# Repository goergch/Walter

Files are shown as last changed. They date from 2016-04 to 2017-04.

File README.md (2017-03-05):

# Walter
Walter is a self-made, dangerous, industrial robot with 6 DOF. Right in the middle of development. Check the [Documentation](http://walter.readthedocs.io). Contact me via the [hackaday page](https://hackaday.io/post/53678).

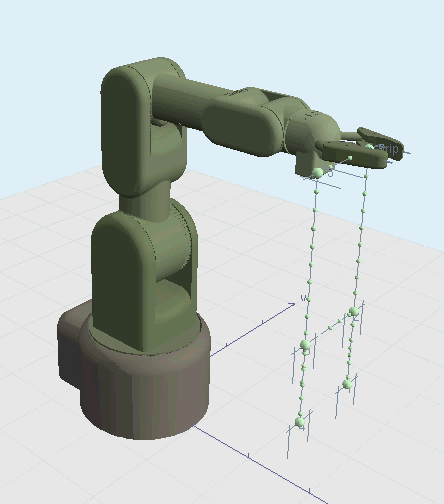
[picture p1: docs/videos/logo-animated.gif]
work in progress


### Contents
    /cad 	    CAD designs (TurboCAD)
    /theory     mainly kinematics
    /code       code of Cortex, Trajectory Planner, and Webserver  
    /schematics schematics of Cortex and its power board
    /docs		source of Walter's [Documentation](https://http://walter.readthedocs.io)
    /datasheets datasheets of components Walter is made of

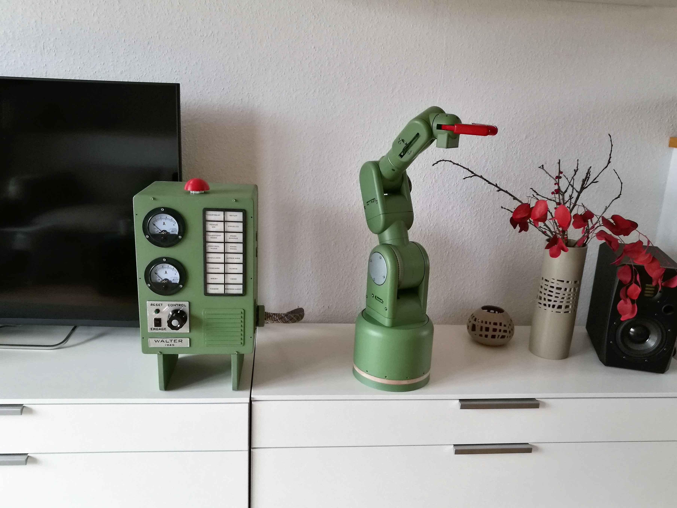
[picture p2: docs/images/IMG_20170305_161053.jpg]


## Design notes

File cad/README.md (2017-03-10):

All CAD  files made with TurboCAD. Due to a performance issue with TurboCAD, the working sources with geometric parts are stored in [intermediate](https://github.com/jochenalt/Walter/blob/master/cad/intermediate). The final objects (ACIS objects only) are stored here. In [simplified](https://github.com/jochenalt/Walter/blob/master/cad/simplified) the objects used within Walters UI (displayed in OpenGL) are located. They omit many details in order to speed up the UI. [Wiki](https://github.com/jochenalt/Walter/blob/master/cad/wiki) contains the CAD explosion drawings used in the documentation.

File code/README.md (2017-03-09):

C++ source code of Walter

* [Cortex](https://github.com/jochenalt/Walter/blob/master/code/BotCortex) 
contains the C++ Teensy code interpolating a given trajectory and running the closed loop for all actuators
* [GLUI](https://github.com/jochenalt/Walter/blob/master/code/GLUI) 
old GLUI framework to enhance openGL by buttons, labels etc.  Used by WalterPlanner.
* [freeglut](https://github.com/jochenalt/Walter/blob/master/code/freeglut) 
old library used by GLUI
* [Common](https://github.com/jochenalt/Walter/blob/master/code/WalterCommon) 
Common parts used by Cortex and Webserver, especially containing the communication protocol in between
* [Kinematics](https://github.com/jochenalt/Walter/blob/master/code/WalterKinematics) 
Library used by Webserver and Planning UI computing kinematics and trajectories
* [WalterPlanner](https://github.com/jochenalt/Walter/blob/master/code/WalterPlanner) 
OpenGL UI for planning trajectories and sending the Webserver
* [WalterServer](https://github.com/jochenalt/Walter/blob/master/code/WalterServer) 
Webserver receiving running on Odroid XU4 receiving commands from WalterPlanner
* [ServerOdroid](https://github.com/jochenalt/Walter/blob/master/code/ServerODroid) 
To be deleted, used before WalterServer was  portable for Windows and Linux

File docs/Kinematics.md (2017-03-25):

Kinematics is about computation of the tool-centre-point (*TCP*) out of joint angles and vice versa. First is simple, latter is more tricky, but lets see later on.
But before starting any kinematics, it is necessary to define all coordinate systems.

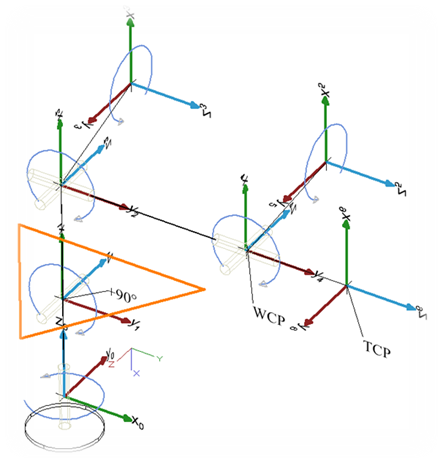
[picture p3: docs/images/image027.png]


The most important design decision is to let the three upper axis’ intersect in one point, the so-call wrist-center-point (*WCP*). This decision makes the computation of the inverse kinematic solvable without numeric approaches.

The picture shows the used coordinate systems in the default position of the bot, having all angles at 0°, starting from the base (angle<sub>0</sub>) and ending with the coordinate system of the hand (angle<sub>6</sub>). For convenience the forearm (angle<sub>1</sub>) adds +90° to the real angle in order to have the base position at 0° of the bot, although the illustrated actually is -90°. The coordinate systems have been are arranged according to the Denavit Hardenberg convention, which is:

The transformation from angle<sub>i</sub> to angle<sub>i+1</sub> is given via 

1. rotation around the x-axis by α

2. translation along the x-axis by α

3. translation along the z-axis by *d*, and

4. rotation around the z-axis by θ

So, the Denavit Hardenberg parameters are:

| Joint | a[°]  | a[mm] | d[mm] |
|---  | ---| --- | --- |
| Hip | *-90°*| *0* | *d<sub>0</sub>* |
| Upper arm  | *0* | *a<sub>1</sub>*  | *0* |
| Forearm | *-90°*| *0* | *0* |
| Elbow | *90°* | *0* | *d<sub>3</sub>* |
| Wrist | *-90°*| *0* | *0* |
| Hand | *0* | *0* | *d<sub>5</sub>* |

The general definition of a Denavit Hardenberg (DH) transformation is

&nbsp;&nbsp;&nbsp;&nbsp;

which is a homogeneous matrix with two rotations *(x,z)* and two translations *(x,z)*.

Combined with the DH parameters, the following DH matrixes define the transformation from one joint to its successor:













## Forward Kinematics

With the DH transformation matrixes at hand, computation of the bot’s pose (i.e the position and orientation of the gripper) out of the joint angles is straight forward. The matrix representing the gripper’s pose  is 

&nbsp;&nbsp;&nbsp;&nbsp; 

By multiplying the transformation matrix with the origin (as homogeneous vector), we get the absolute coordinates of the tool centre point in world coordinate system (i.e. relative to the bot’s base).

&nbsp;&nbsp;&nbsp;&nbsp;

The orientation in terms of roll/nick/yaw of the tool centre point can be derived out of by taking the part representing the rotation matrix (). ([Wikipedia Roll/Nick/Yaw](https://de.wikipedia.org/wiki/Roll-Nick-Gier-Winkel#Berechnung_aus_Rotationsmatrix) )

&nbsp;&nbsp;&nbsp;&nbsp;

&nbsp;&nbsp;&nbsp;&nbsp;  
&nbsp;&nbsp;&nbsp;&nbsp;  
&nbsp;&nbsp;&nbsp;&nbsp;  

For  we have a singularity (*atan2* never becomes this), but wikipedia has a solution for that as well
	
&nbsp;&nbsp;&nbsp;&nbsp;
&nbsp;&nbsp;&nbsp;&nbsp;

if  we get

&nbsp;&nbsp;&nbsp;&nbsp;
&nbsp;&nbsp;&nbsp;&nbsp;

Note: Unfortunately, the gripper’s coordinate system is not appropriate for human interaction, since the default position as illustrated in the [Coordinate Systems](images/image027.png) is not nick/roll/yaw=(0,0,0). So, in the Trajectory Visualizer it is handy to rotate the gripper matrix such that the default position becomes (0,0,0). The according rotation matrix represents a rotation of -90° along *x*,*y*, and *z*, done by the rotation matrix

&nbsp;&nbsp;&nbsp;&nbsp;

In the following equations, this is not considered, since it is for convenience in the UI only, so you will find that additional rotation in the source code only. 

## Inverse Kinematics 
Inverse kinematics denotes the computation of all joint angles out of the tool-centre-point’s position and orientation. In general this is hard, and giving a non iterative solution for a 6DOF robot is only feasable, when computation of the grippers position and the grippers orientation can be considered separately, i.e. the angles of the lower three actuators is not depending on the orientation of the gripper. Still, I do not like numerical solutions, even though with todays processors (or FPGAs) this is no more a question of computational power. I just think that a numerical solution is not a real solution but a surrender to complexity. That's why I let the upper three joint angles intersect in the WCP, which is a basic assumption of the following. 

Input of inverse kinematics is the TCP’s position and orientation in terms of roll, nick, yaw, abbreviated by *γ*, *β*,and *α*.





First, we need to compute the wrist-centre-point out the tool-centre-point. This is possible by taking the TCP and moving it back along the TCP’s orientation by the hand length. For doing so, we need the transformation matrix from the base to the last joint  
which we can derive out of the TCP’s position and orientation.

To build the transformation matrix  we need the rotation matrix defining the orientation of the TCP. This is given by multiplying the rotation matrixes for all axis (*γ*, *β*, *α*) which gives  (see also *[computation of rotation matrix out of Euler Angles](http://kos.informatik.uni-osnabrueck.de/download/diplom/node26.html)*).

&nbsp;&nbsp;&nbsp;&nbsp;

Now we can denote the transformation matrix of the TCP by building a homogenous matrix out of *TCP<sub>orientation</sub>* and *TCP<sub>position</sub>*:

&nbsp;&nbsp;&nbsp;&nbsp;

From the TCP’s perspective, WCP is just translated by *d<sub>5</sub>*:

&nbsp;&nbsp;&nbsp;&nbsp;

Furthermore, , so we get the WCP by

&nbsp;&nbsp;&nbsp;&nbsp;

in world coordinates.

Having a top view on the robot shows how to compute the first angle *θ<sub>0</sub>*:

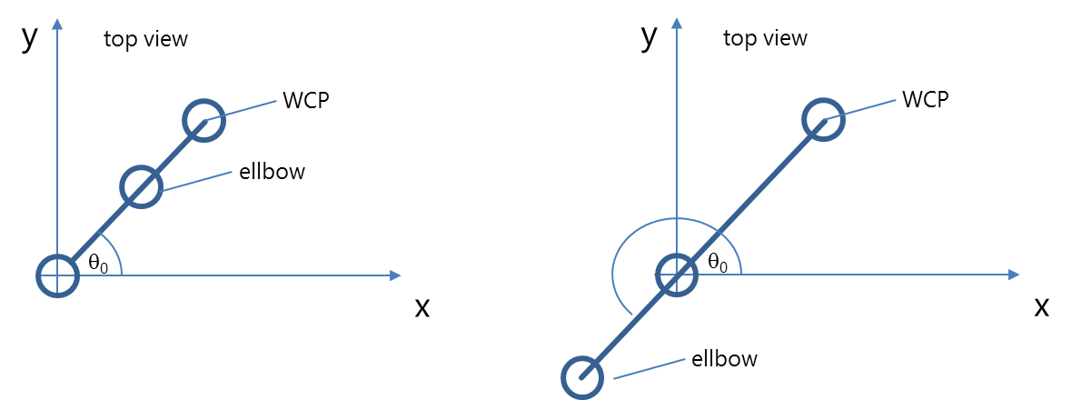
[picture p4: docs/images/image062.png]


&nbsp;&nbsp;&nbsp;&nbsp;

Actually, this angle exists in two variants: if the bot looks backwards, we get the formula above. But another valid solution is looking backward when we get 

&nbsp;&nbsp;&nbsp;&nbsp;

Thanks to the design having a wrist-centre-point where the axes of the three upper actuators intersect, the next two angles can be computed by the triangle denoted in orange:



Again, there are two solutions (aka configurations), one configuration corresponds with a natural pose of the elbow, solution II is a rather unhealthy position:

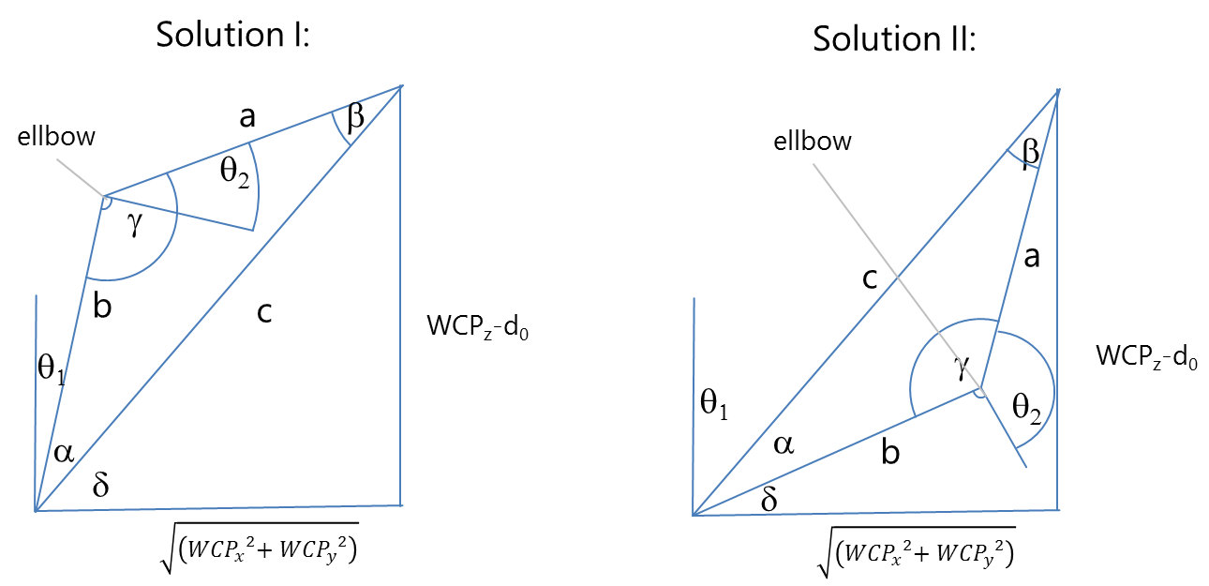
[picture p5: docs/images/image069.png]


*a* and *b* is given by the length of the actuators *a<sub>1</sub>* und *d<sub>3</sub>*. So, with cosine law we get the angles *α* and *γ*.

&nbsp;&nbsp;&nbsp;&nbsp;

&nbsp;&nbsp;&nbsp;&nbsp;
	
Finally, we get


	

and the second solution 

&nbsp;&nbsp;&nbsp;&nbsp;
&nbsp;&nbsp;&nbsp;&nbsp;	

The upper angles *θ<sub>4</sub>*, *θ<sub>5</sub>*, *θ<sub>5</sub>* can be obtained by considering the chain of transformation matrixes. With

&nbsp;&nbsp;&nbsp;&nbsp;	

we get

&nbsp;&nbsp;&nbsp;&nbsp;	

To ease the annoying multiplication  we only need to consider the rotation part of the homogenous matrixes, translation is no more relevant, since the orientation alone defines the three upper angles. 

&nbsp;&nbsp;&nbsp;&nbsp;	

 - and therefore the rotation part  - is already known resp. can be obtained out of the given angles *θ<sub>0</sub>*, *θ<sub>1</sub>*, *θ<sub>2</sub>* by
	
&nbsp;&nbsp;&nbsp;&nbsp;	

By equalizing the previous two equations we get a bunch of equations defining the upper angles, still these equations are hard to solve, due to the complex combination of trignometric functions. But, there are some equations which are simpler and can be solved for an angle. First angle that seems to be easily computable is *θ<sub>4</sub>*:

&nbsp;&nbsp;&nbsp;&nbsp;	

gives two solutions

&nbsp;&nbsp;&nbsp;&nbsp;	

For *θ<sub>3</sub>* there is no easy matrix element, but we can combine

&nbsp;&nbsp;&nbsp;&nbsp;	
&nbsp;&nbsp;&nbsp;&nbsp;		

to

&nbsp;&nbsp;&nbsp;&nbsp;		

which ends up in

&nbsp;&nbsp;&nbsp;&nbsp;		

again having two solutions depending on *θ<sub>4</sub>*. Same is done on *θ<sub>5</sub>*:

&nbsp;&nbsp;&nbsp;&nbsp;		

If *θ<sub>4</sub>=0*, we have an infinite number of solutions *θ<sub>3</sub>* and *θ<sub>5</sub>* (gimbal lock). In that case, we consider   :		

&nbsp;&nbsp;&nbsp;&nbsp;.		

Since we know the trigonometric addition theorem from school

&nbsp;&nbsp;&nbsp;&nbsp;		

we get

&nbsp;&nbsp;&nbsp;&nbsp;		

We are free to choose *θ<sub>3</sub>* and arbitrarily select the bot’s current angle *θ<sub>3</sub>*, such that this one will not move in that specific case.

&nbsp;&nbsp;&nbsp;&nbsp;		
 
In the end, we get eight solutions by combining the possible pose configurations of  *θ<sub>0</sub>*(forward/backward), *θ<sub>1</sub>* and *θ<sub>2</sub>*(triangle flip), and *θ<sub>4</sub>*(hand orientation turn).

The correct solution is chosen by taking the one that differs the least from the current bot’s joint angles. 
What is with all the other equations from ? We could use them to invalidate some of the four solutions, but still there will remain a list of solutions we need to choose from. So, it does not really make sense to take this route.

The selection algorithm is quite simple:

1. consider only mechanically valid solutions, i.e. omit those that violate mechanical boundaries.

2. Compute an angle-wise "*distance*" to the current position and take the solution with the least distance, i.e. take the solution with the least movement.

The latter has the consequence that the pose will try to remain in a configuration and no sudden movements like a turn of 180° happens.

All this is implemented in [Kinematics.cpp](https://github.com/jochenalt/Walter/blob/master/code/WalterKinematics/src/Kinematics.cpp). But - as usual - trying out before implementing this is a good idea, so I did that in this [spreadsheet](https://github.com/jochenalt/Walter/blob/master/theory/Kinematik.xlsx).

Speaking of configurations: if you want to change the configuration of the bot, e.g. from elbow down to elbow up which includes turning the base by 180° the approach of having a linear movement from one pose to the other and interplating in between does not work anymore, since the start and end poses are identical, but with a different configuration.

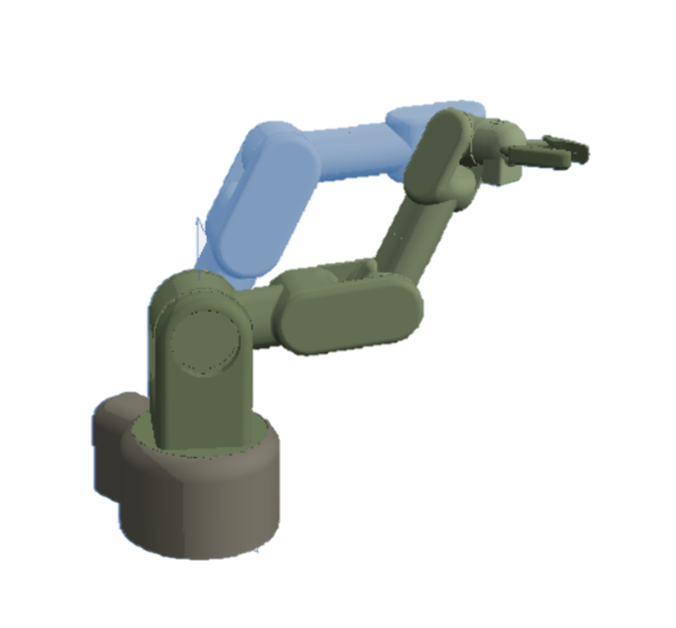
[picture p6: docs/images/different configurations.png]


First possibility to change configuration is to have a non-linear movement that interpolates angle-wise resulting in a weired movement that would be really dangerous in a real world:

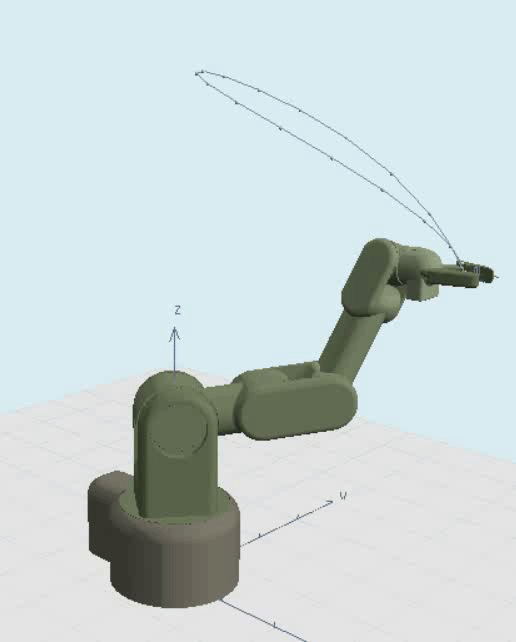
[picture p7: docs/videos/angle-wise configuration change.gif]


So, you rather introduce an intermediate pose where you can safely turn the critical actuator (mostly the shoulder). This is not less expansing, but a more controlled way:

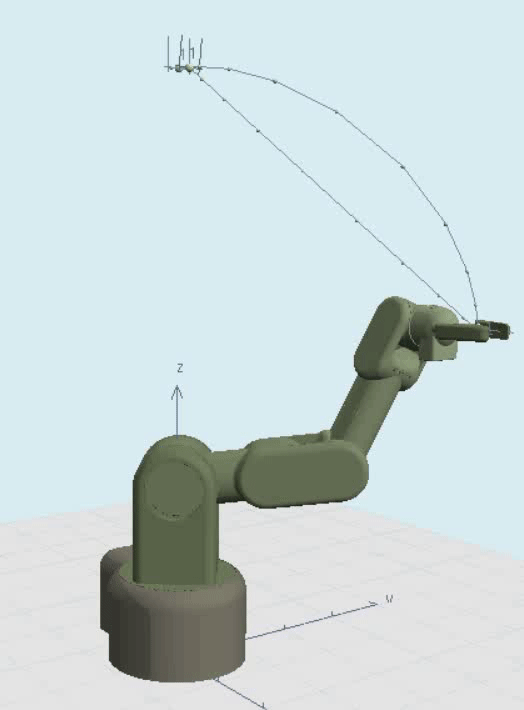
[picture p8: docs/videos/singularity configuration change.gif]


Thing is, that one has to go via a singularity (the upright position) which is normally avoided like hell. One reason is the way how we compute *θ<sub>4</sub>=0*, and a numerical reason that singularities are kind of a black hole, the closer you get, the more you are sucked into imprecisions of floating numbers since you approach poles of the underlying functions. So it is defininitely best to simply avoid changing configurations or getting too close to singularities.

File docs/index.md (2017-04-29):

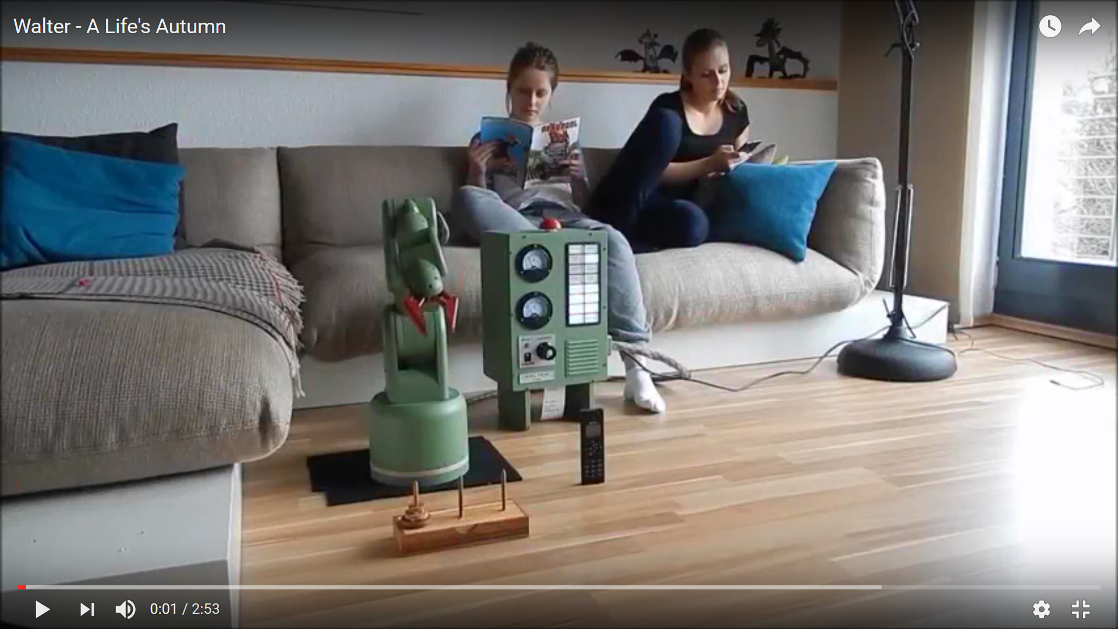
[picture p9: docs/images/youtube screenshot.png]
(http://www.youtube.com/watch?v=XK3WcrrcC8U)


Since man built the first robot, he wanted it to look like himself. I want to make Walter look vintage, and as little DIY as possible, so no visible humps or bulges with motors or gearboxes, nor horrible cables hanging everywhere. Reminds me too much of my dentist. 

Most of the DIY robots are using servos, mostly for convenience, since the encoder is built-in already and they are easy to control. Thing is, when it comes to higher torque, the connection of the servo with the actuator becomes difficult, and hard to make of 3D printed material. If the servo or the flange moves just a little bit within the housing, the according play will magnify to a significant amount at the end of the actuator. An The required precision to avoid this is way above hobby grade components. 


And servos are boringly easy to use. No fun in construction. A motor with a belt drive and a separate angle sensor solves this, it provides low backlash and allows the electronics to compensate imprecise parts with the sensor placed separately from the motor. Additionally, the motor of an actuator can be placed in the previous joint, lowering the centre of gravity of each actuator.

When a belt drive is set, choice comes naturally to stepper motors, since an additional gearbox is not necessary anymore, torque is high and the belts should compensate the vibrations coming from the stepping nature of these motors.

I started with an openGL application simulating the construction.

Now, Walter looks like this, in a beautiful arrangement with selected flowers:


Software part is not easy and especially time-consumung. Most robot makers stop as soon as the limps are moving, which always looks unfinished. But, making the full stack including trajectory planning means four months of work when you have weekends only, of which some parts are really difficult (inverse kinematics). The data flow of the full stack looks like this:

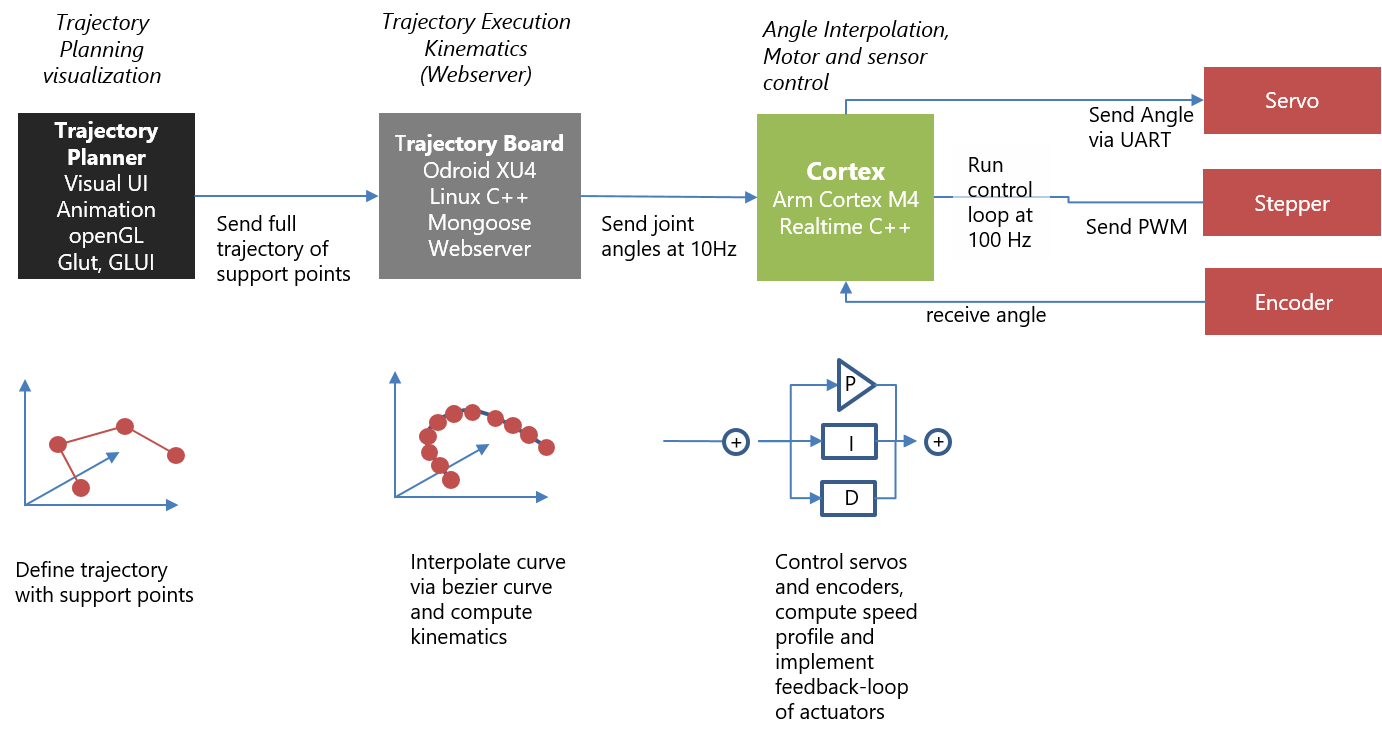
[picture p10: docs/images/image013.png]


We have:

* [Trajectory Planner](./Trajectory) ([source code](https://github.com/jochenalt/Walter/tree/master/code/WalterPlanner))
This is a UI for planning trajectories. All animated gifs in this wiki are made with it. Trajectories are planned by defining single support points. After planning is done, the trajectory is transfered to the

* [Trajectory Execution](./Webserver) ([source code](https://github.com/jochenalt/Walter/tree/master/code/WalterServer)). This component consists of a webserver that runs trajectories by interpolating Bézier curves betweeen support points, computing the inverse [Kinematics](https://github.com/jochenalt/Walter/wiki/Kinematics) per pose and sends the resulting series of angles to the 

* [Cortex](./Cortex) ([source code](https://github.com/jochenalt/Walter/tree/master/code/BotCortex)). This low level component takes interpolated poses and controls the actuators accordingly by applying control algorithms ([PID controller](https://en.wikipedia.org/wiki/PID_controller)). Servos are controlled directly by the cortex controller board  via a serial interface. Steppers do not have an internal feedback loop, so we need rotary encoders detecting the absolute angle of the joint and allowing to implement feedback controllers.

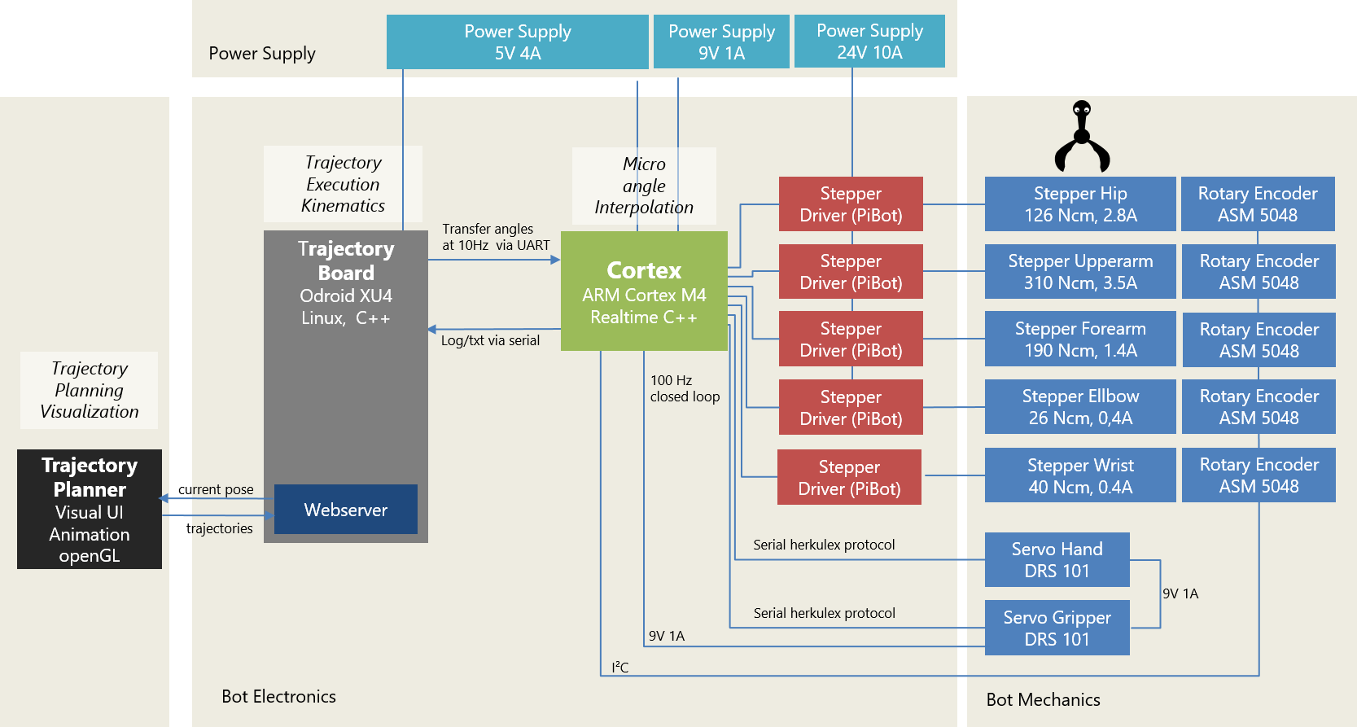
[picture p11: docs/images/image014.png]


On the mechanical side, we have two actuators driven by a servo (mainly due to space restrictions) and five actuators driven by a stepper/rotary encoder combination. Details are shown in [Construction](./Construction).

Steppers are driven by 3D-printer components (PiBot Stepper Driver) around the popular IC Toshiba 6600 (4.5A max). The stepper drivers are directly connected to the Cortex receiving joint angles at 10Hz, interpolating the points in between, and sending the according PWM signal to the stepper drivers and to the servos. Besides micro interpolation of the trajectory, the controller board takes care of the speed profile, i.e. it limits the acceleration and speed of each actuator. The controller board is a DIY PCB around an ARM Cortex M4 (Teensy 3.5), running the control loop with 100 Hz. I started with an ATmega 644, but it turned out that the ATmega was not able to control 5 steppers with a proper sample rate, let alone reading 5 encoders on top (in a previous project I solved that by using 16-bit fixed point arithmetics instead of floating point, which gave a performance boost but ended up in a mess of source code).

The trajectory controller board is encapsulated by a webserver exposing the current movement and accepting commands like new trajectories.

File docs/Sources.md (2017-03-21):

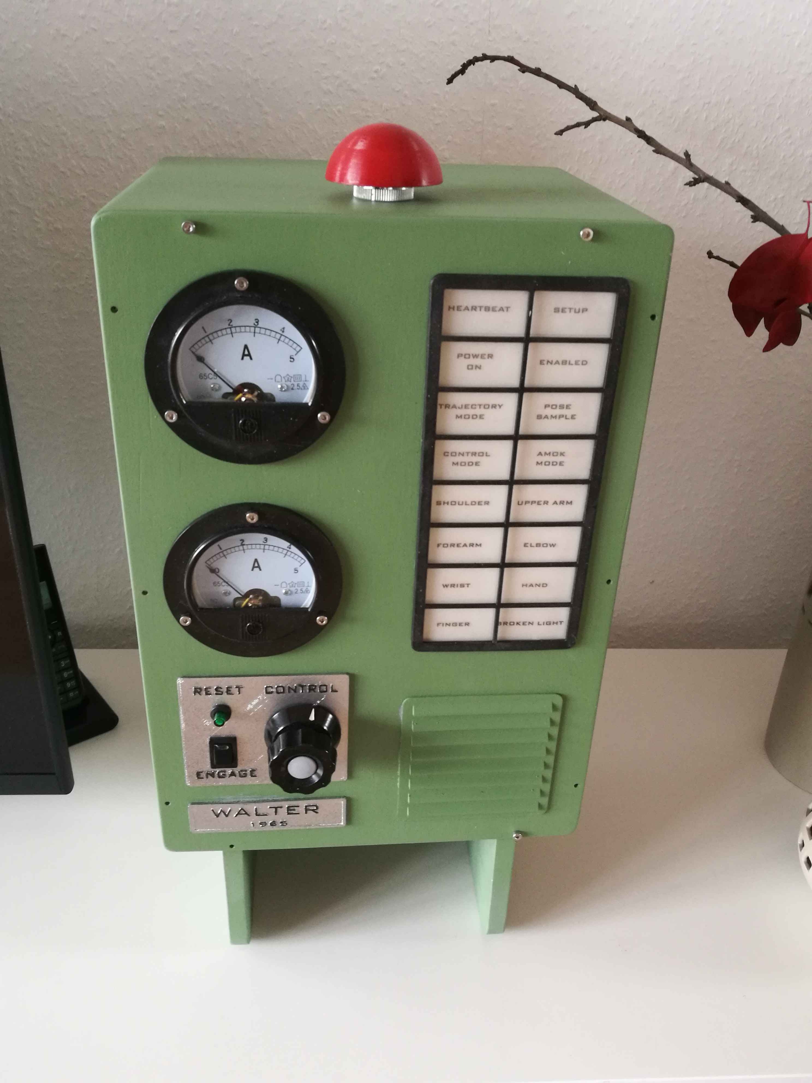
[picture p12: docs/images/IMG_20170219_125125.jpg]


## Download Links

* [CAD Models](https://github.com/jochenalt/Walter/tree/master/cad)
Designs made with TurboCAD, used to 3D-print all parts
* [Schematics](https://github.com/jochenalt/Walter/tree/master/schematics)
Cortex and Power Supply PCB made with KiCAD
* [Source Code](https://github.com/jochenalt/Walter/tree/master/code)
C++ code of Cortex, Trajectory Planner, and Webserver  
* [Datasheets](https://github.com/jochenalt/Walter/tree/master/datasheets)
Datasheets of components Walter is made of
* [Zip](https://github.com/jochenalt/Walter/archive/master.zip)
Give me everything

## Contact 

Please contact me via my [hackaday](https://hackaday.io/project/19968-walter) page.

## FAQ

### 3D print
I used the Zortrax M200 printer with Z-ultrat, a high-temperature ABS. For all parts besides plugs and belt spanners and gears I applied the  parameters 0,14mm resolution, 4 layers wall thickness and 15% infill. For the latter, I used 50% infill. All in all, Walter required ca. 2kg filament.

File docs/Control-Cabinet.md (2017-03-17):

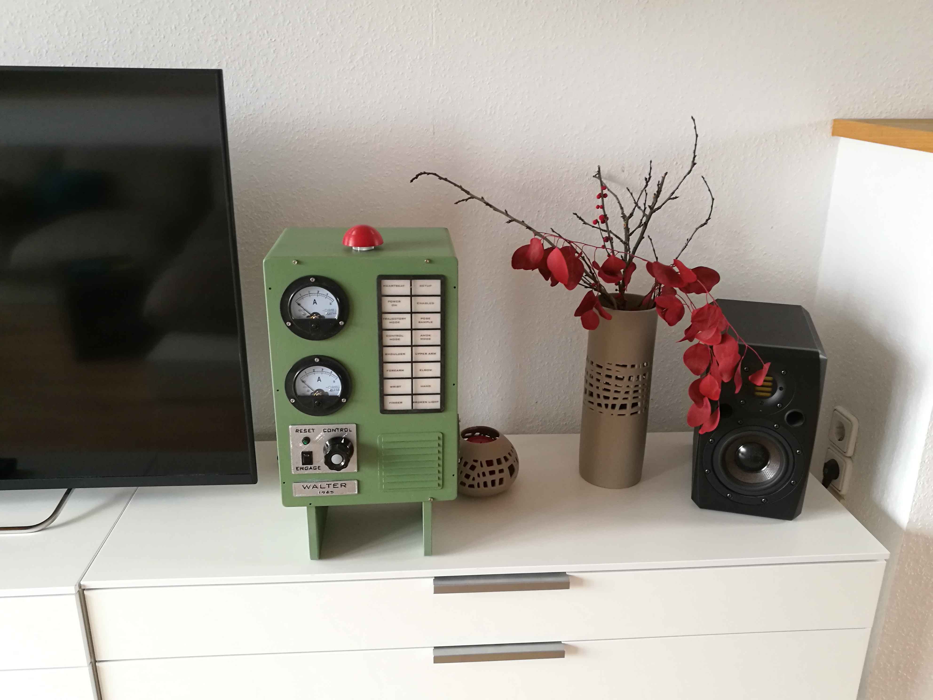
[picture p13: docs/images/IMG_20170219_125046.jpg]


Here we see the control cabinet in its natural environment, accompanied by a japanese flower arrangement. The inners is a scaffold for the power supply, the stepper drivers, and some smaller PCBs.

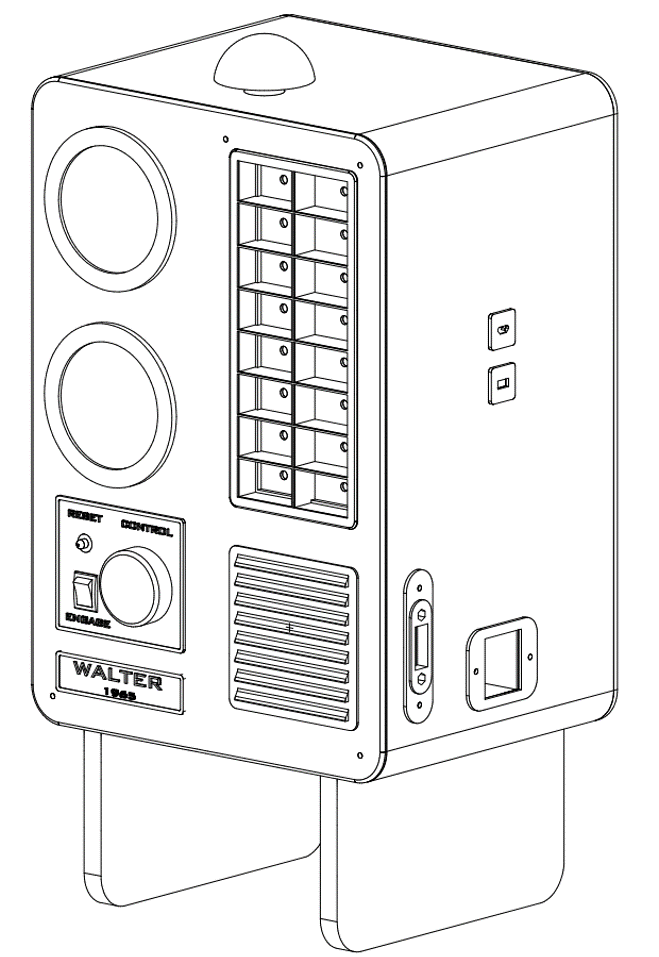
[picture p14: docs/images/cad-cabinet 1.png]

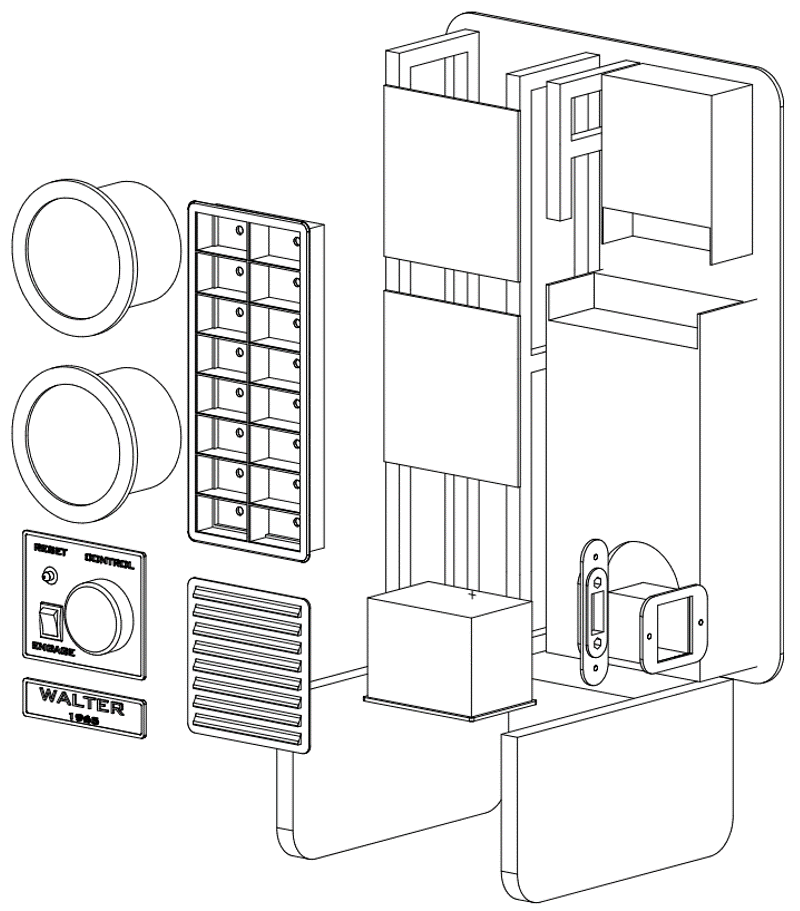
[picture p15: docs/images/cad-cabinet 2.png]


I tried to give it a GDR-vintage-style, mostly by having these great round panel meters (I got via ebay from China) and a panel of mostly useless lamps. 

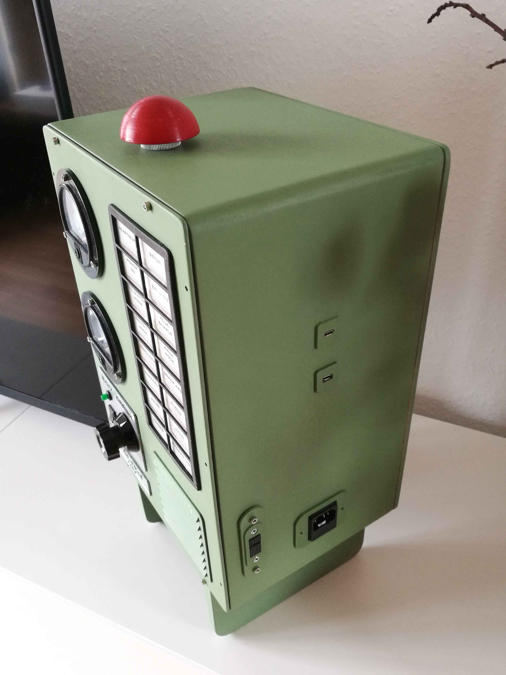
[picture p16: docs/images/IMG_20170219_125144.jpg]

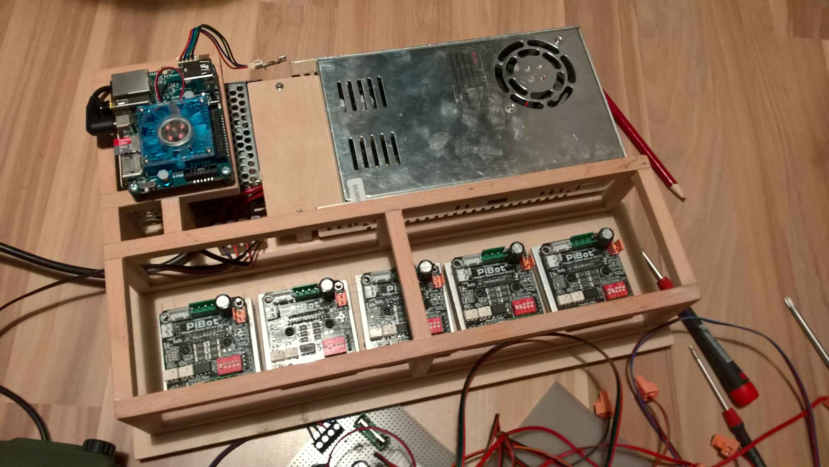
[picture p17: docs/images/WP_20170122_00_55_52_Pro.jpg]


All sockets are on the left side of the wooden box, biggest socket is for the fat 28-pin cable containing lines for the steppers, encoders and servos. Above there are two USB ports, one for the serial interface of the Odroid XU4, which is handy if Wifi is not working, and one for the Teensy (Walter's Cortex). Power supplies are fixed on the backside with screws, the scuffold for electronics is glued to the back side. The picture on the right shows the tidy version of the inners with power supplies and stepper drivers only. When the other PCBs are added and all the cabeling is done, you better close the box. On top of the box a nice emergency stop button is placed.

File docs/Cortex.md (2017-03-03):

Assuming that we have the trajectory defined in terms of a sequence of joint angles, we still need to translate that into movements of the motors. This translation should be done in a manner that no motors limits are violated, and with a speed profile that avoids vibrations by limiting the acceleration. 

Additionally, we need a feedback loop to ensure that the to-be angle of the motor is actually reached.

All this is done in Walters Cortex, a board based on an 32-bit ARM microcontroller (Teensy 3.5) that receives interpolated trajectory points at 10Hz, and runs a closed loop for the stepper motors at 100Hz. In that closed loop, the encoders are sampled reading the angle of each actuator with a precision of 14-bit = 0.02° generateing stepper impules that follow the trajectory. Furthermore, it takes care that no bumpy movements happen by limiting angle, speed, and acceleration. This should have happened during trajectory planning already, but you never know.

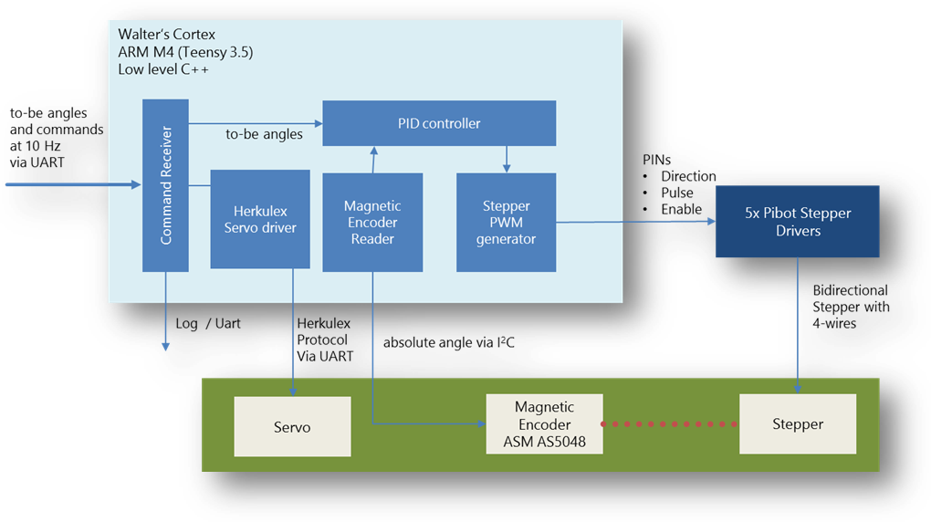
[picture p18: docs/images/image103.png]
		

## Schematics

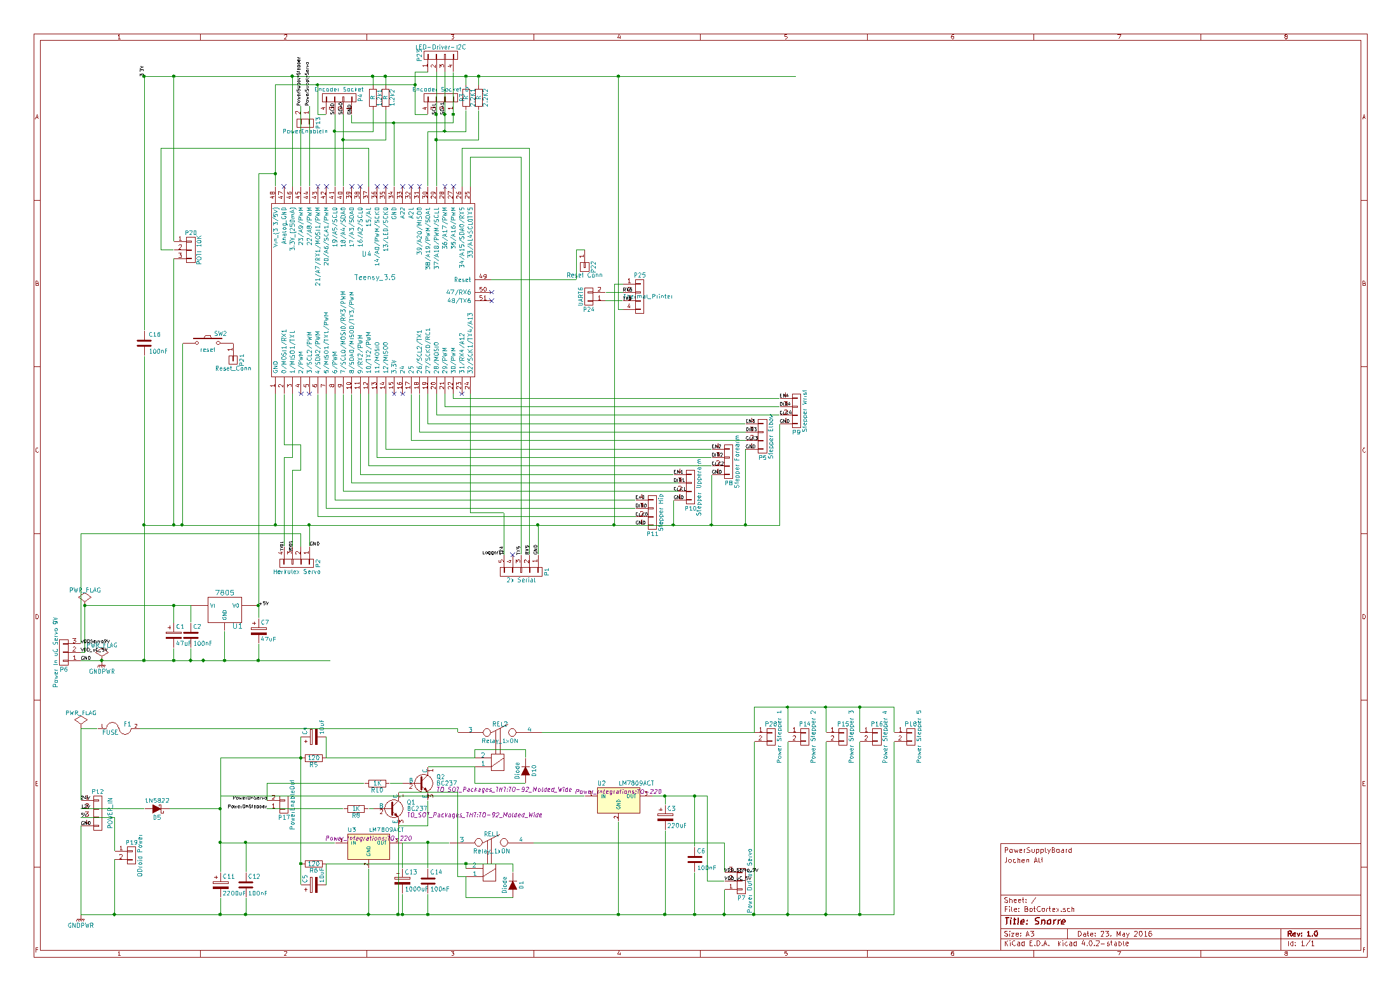
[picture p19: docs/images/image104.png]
		

The lower part of the layout contains a separate power supply for the servos, the steppers and mC. The mC gets 5V by a standard integrated voltage regulator (7805), the two servos are driven by a 7809 voltage regulator providing 2A (two HerkuleX servos required 1A at most). Additionally, there are two relays for a proper start-up procedure switching the 240W power supply for the steppers and the power supply for the servos. This has been necessary to avoid impulses to the motors inducing annoying ticks when power is switched on.  So, after booting the Trajectory Board and switching on the Cortex, all steppers are disabled, afterwards the steppers power supply is turned on, then the servos power supply is switched on. By that procedure, no ticks are happening during starting up.

On top there is the Arm Cortex M4 controller. As usual, tricky part was to provide a stable power supply for all components. I struggled a lot with pikes induced by the strong steppers; particularily the magentic encoders respond very sensitive to voltage.

So, I made a separate board providing 24V/10A for the steppers (kind of overpowered, 6A would have been sufficient as well), 5V 4A for the Odroid XU4 and the Teensy 3.5, and 9V 2A for Herkulex servos. Servo’s and stepper’s power supply are turned on by a relay. 

This is the PCB layout, which turned out to be rather simple. Especially the Teensy part consists more or less of sockets only:

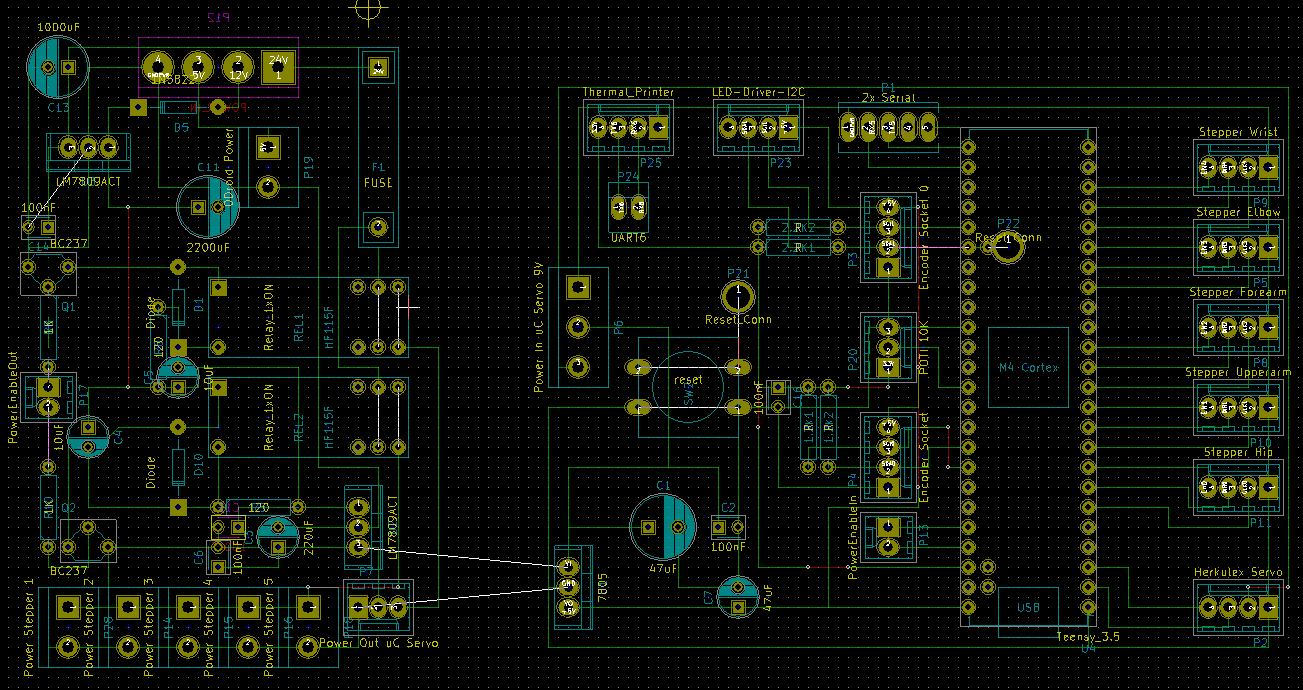
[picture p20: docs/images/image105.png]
		

Putting all together looks like this:

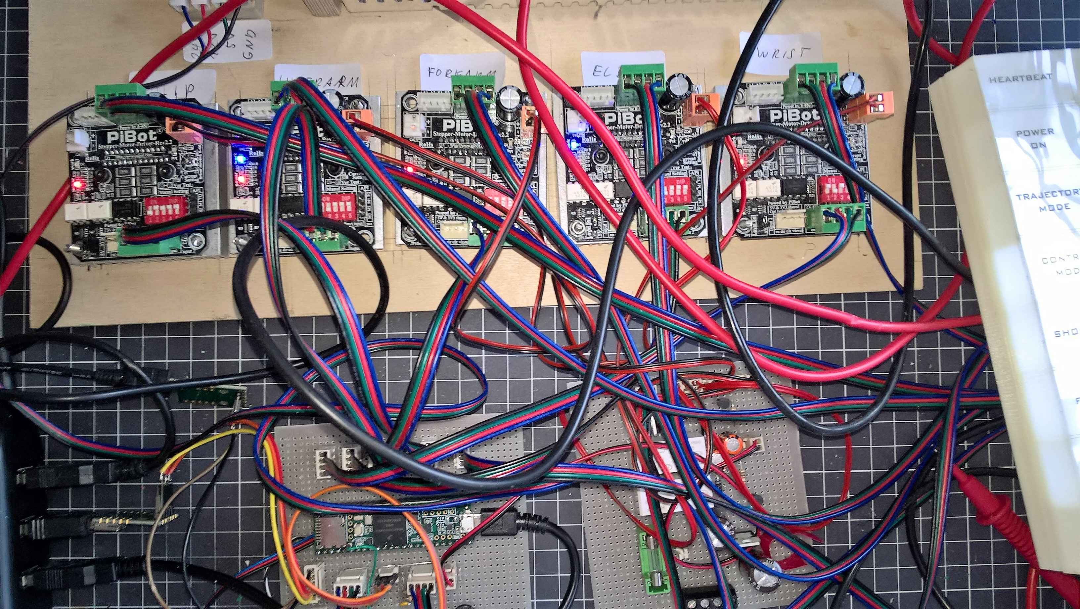
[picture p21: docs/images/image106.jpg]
		

This is my desk with 5 Pibot drivers, a Teensy 3.5 (on the left bottom side)  and the power supply PCB on the right. The wooden board is the backside of the [control cabinet](./Control-Cabinet)

## Sensors

The used sensors are AMS' magnetic encoders 5048B with 14-bit resolution and an I2C interface. They are driven 3.3 V on two I2C buses. Walter has no electronics in its base, all is connected via a long cable of approx. 1.5m. In general, this is a bad idea, since the capacity of that cable  alone is around 250pF. So, I had to use  small pullup resistors of 1.1K&#x2126; for both I2C lines (see also [Computation of I2C pullup resistors](http://www.ti.com/lit/an/slva689/slva689.pdf) to get sharp impulses on the I2C bus. Minimum is around 966&#x2126; to not exceed 3mA in SDA/SCl lines.

## Software 
The software of the Cortex runs on the basis of the Arduino library. This is a legacy, since I started with an 8-bit ATmega controller before I upgraded to an Arm processor (This happened when I realized that controlling 5 steppers and encoders eats up much more computing power than I thought). The software is interfaced via UART and accepts these commands (most important selection):

`SETUP [force]`  
*Initializes steppers, drivers, encoders and servos. Does an initial calibration.
If not successful, power is switched off. If parameter force is used, this does 
not happen, but everyhting initialized successfully is waiting for commands*

`POWER (on|off)`  
*Turns on/off power of steppers and servos*

`ENABLE`  
*Enables steppers, i.e. gives power to them assuming "power on" has been issued
already*

`MOVETO <angle1> <angle2> <angle3> <angle4> <angle5> <angle6> <angle7> <durationMS>`  
*Moves the bot (assuming power is on and it has been enabled) to the given angles 
within passed amount of time. This service is called at 10Hz by the trajectory 
execution module (webserver).*

`GET all -> {<ActuatorNo> : n=<name> ang=<angle> min=<min> max=<max> null=<null>}`  
*Returns the current state of the bot as a list return angle, min, max and null 
value per actuator.*

## Steppers

While controlling robot servos is easy (everything is built in, even a PID controller, they only require a serial interface and a library), stepper motors are more difficult to control. While very tempting by providing high torque without a gearbox and a proper position even without encoders, they turned out to cost me many hours until they moved that smooth as expected.

First approach was the classical feed-back control system taking the encoder angle and the to-be angle of an actuator, giving that to PID controller, computing a correcting angle and giving that to the stepper motor. In the Arduino space, the standard library to control steppers is AccelStepper  which can be used to implement that and leverage from the nice feature of smooth acceleration and deceleration.

This idea was bad. AccelStepper provides the method move(targetposition) that accelerates first and decelerates afterwards until the motor stops exactly at the targetposition. This works fine for larger moves of several seconds. But in a closed loop, this permanent acceleration and deceleration produced vibrations ending up in resonances. Speed was very limited not to mention a nasty sound.

The solution that finally worked was to compute the acceleration that is required in one sample of 10ms, and set this acceleration explicitly for the next sample:

&nbsp;&nbsp;&nbsp;&nbsp;		

*v<sub>encoder</sub>* is the speed that is necessary to compensate lost steps. It can be approximated by

&nbsp;&nbsp;&nbsp;&nbsp;		
   
Unfortunately, setting the acceleration requires a square root for computing the time until the next step (as done internally in AccelStepper)

&nbsp;&nbsp;&nbsp;&nbsp;		

This equation was the reason to decommission the previously used 8-bit Atmega and go to a 32-bit ARM processor with FPU which provides the square root computation in hardware.

The final closed-loop looks like this:

```
    void stepperLoop () {
    	float dT = sampleTime();                         // [ms], approx. 10ms
    	float currentAngle =        getEncoderAngle();   // encoder value in [°]

   	    // interpolate trajectory to get current and next angle
    	float toBeAngle =           movement.getCurrentAngle(millis());
    	float nextToBeAngle =       movement.getCurrentAngle(millis()+dT);

   	    // get speed of current sample, next sample and error compared to encoders angle
    	float currStepsPerSample =  getMicroStepsByAngle(toBeAngle - lastToBeAngle);
    	float nextStepsPerSample =  getMicroStepsByAngle(nextToBeAngle - toBeAngle);
    	float stepErrorPerSample =  getMicroStepsByAngle(toBeAngle  - currentAngle);  

   	    // implement PI controller. kP is 0.3-0.5, kI can be low (< 0.1) depending on mechanics
    	float Pout = kP * stepErrorPerSample;
    	integral += stepErrorPerSample * dT;
    	float Iout = kI * integral;
    	float PIDoutput = Pout + Iout;
    	float accelerationPerSample = PIDoutput;
    	float distanceToNextSample = accelerationPerSample + currStepsPerSample;
    	
        // compute the acceleration for this sample
    	float sampleAcc = ((currStepsPerSample-nextStepsPerSample+stepErrorPerSample) / dT;
    	accel.setAcceleration(fabs(sampleAcc));      // do not accelerative faster than sampleAcc
    	accel.move(distanceToNextSample);            // move n steps
    }
```

Source code is in [WalterCortex](https://github.com/jochenalt/Walter/tree/master/code/BotCortex), control loop above can be found in [GearedStepperDriver.cpp](https://github.com/jochenalt/Walter/blob/master/code/BotCortex/GearedStepperDrive.cpp).

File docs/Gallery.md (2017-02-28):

Welcome to Walters **Gallery**!

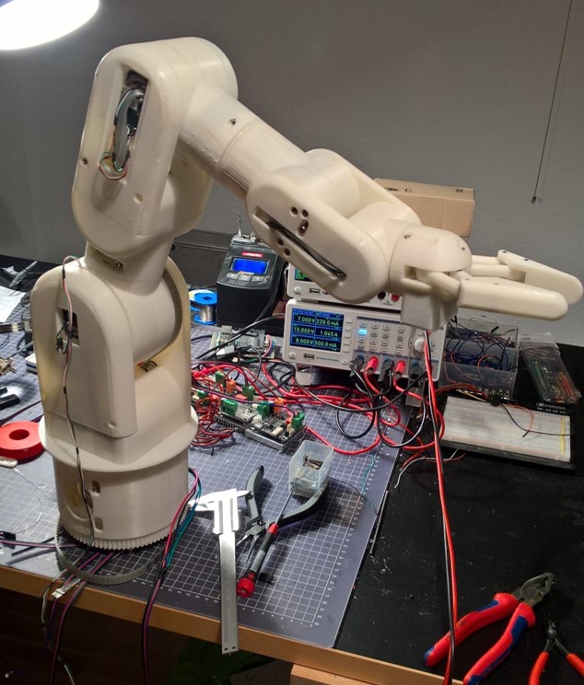
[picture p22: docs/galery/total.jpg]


<table>
    <tr valign="top">
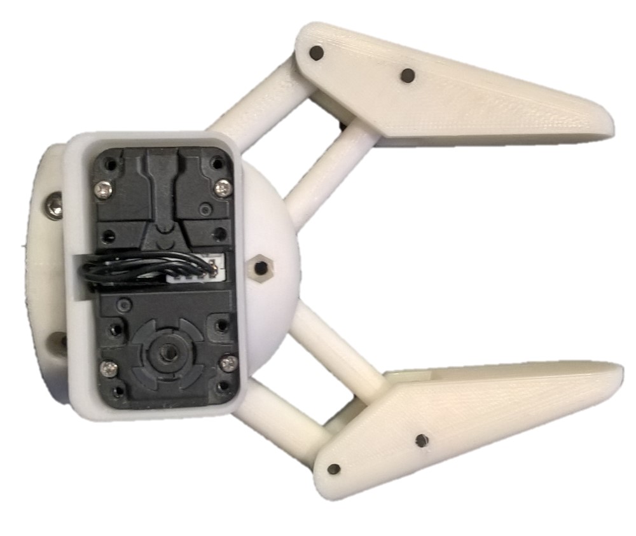
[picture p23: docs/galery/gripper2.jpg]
        <td width="25%">Gripper<br></td>
        <td width="25%">Gripper<br></td>
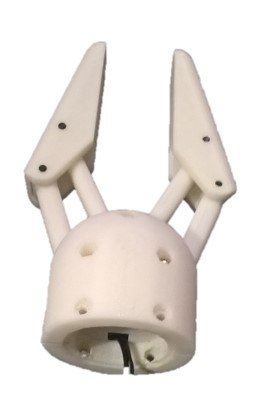
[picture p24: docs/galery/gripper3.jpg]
        <td width="25%">Gripper<br></td>
    </tr>
    <tr valign="top">
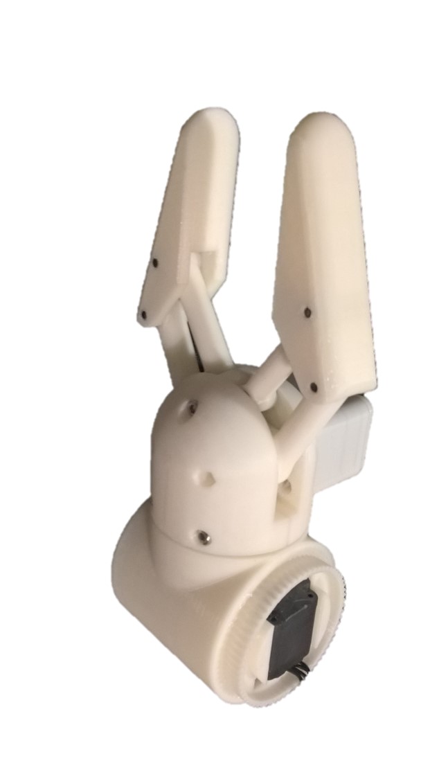
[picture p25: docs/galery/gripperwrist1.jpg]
        <td width="25%">Gripper/Wrist<br></td>
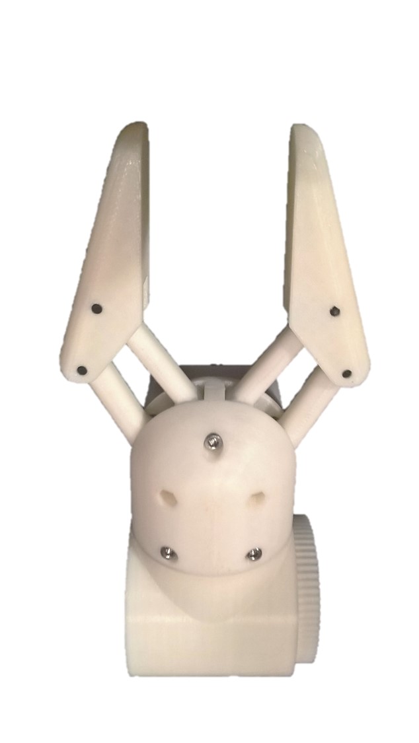
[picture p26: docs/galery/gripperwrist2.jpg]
        <td width="25%">Gripper/Wrist<br></td>
        <td width="25%">Wrist<br></td>
   </tr>
   <tr valign="top">
        <td width="25%">Forearm rotary encoder<br></td>
        <td width="25%">Forearm inside<br></td>
        <td width="25%">Forearm outside<br></td>
   </tr>
   <tr valign="top">
        <td width="25%">Elbow flange with magnet for encoder<br></td>
        <td width="25%">Elbow inside<br></td>
        <td width="25%">Elbow gearbox<br></td>
   </tr>
   <tr valign="top">
        <td width="25%">Upperarm <br></td>
        <td width="25%">Upperarm<br></td>
        <td width="25%">Upperarm<br></td>
   </tr>
   <tr valign="top">
        <td width="25%">Shoulder<br></td>
        <td width="25%">Shoulder<br></td>
        <td width="25%">Shoulder<br></td>
   </tr>

</table>

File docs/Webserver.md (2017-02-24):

Trajectory Execution is done in a webserver that accepts a trajectory from the [Trajectory Planner](./Trajectory). The sent trajectory is *compiled* already, i.e. all intermediate points with a sample rate of 10Hz have been computed, speed profile is applied and inverse [kinematics](./Kinematics) has been precomputed.

So, the webservers receives a long list of interpolated poses including all actuator angles and all the timing information.
The webserver has the simple job of running the trajectors by sending the interpolated points with the correct timing to the [Cortex](./Cortex). It is implemented with [Mongoose](https://www.cesanta.com). 

In addition to its main task, it provides a webpage for debugging purposes, where direct commands to the cortex can be entered. Since the Cortex does not unterstand poses but expects actuator angles, the webserver is able to run the kinematics as well, especially during startup and teardown, when the Walter will move to its default position.

This webpage is done with [Webix](http://webix.com), a small JS-Framework and implemented in [index.html](https://github.com/jochenalt/Walter/blob/master/code/WalterServer/web_root/index.html). The Webserver can be found [here](https://github.com/jochenalt/Walter/tree/master/code/WalterServer).



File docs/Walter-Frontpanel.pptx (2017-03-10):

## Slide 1

Printout of Control Cabinet Frontpanel

Heartbeat

Setup

Power
On

Enabled

Trajectory
MODE

Pose
sample

Control
MODE

AMOK
Mode

Shoulder

Upper arm

Forearm

Elbow

Wrist

Hand

Finger

Broken
light

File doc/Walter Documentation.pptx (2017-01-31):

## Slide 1

WALTER

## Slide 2

WALTER

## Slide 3

Power Supply

Power Supply
5V 4A

Power Supply
9V 1A

Power Supply
24V 10A

Trajectory
Planning
visualization

Visual UI
Animation
openGL

Trajectory
Execution
Kinematics

Trajectory Board
Odroid XU4
Linux, C++

Micro
angle
Interpolation

Controller Board
ARM Cortex M4
Realtime C++

100 Hz
closed loop

Stepper
Driver (PiBot)

Stepper Hip
126 Ncm, 2.8A

Rotary Encoder
ASM 5048

Transfer angles
at 10Hz via UART

Stepper
Driver (PiBot)

Stepper Upperarm
310 Ncm, 3.5A

Rotary Encoder
ASM 5048

Log/txt via serial

Serial herkulex protocol

Serial herkulex protocol

Stepper
Driver (PiBot)

Stepper
Driver (PiBot)

Stepper
Driver (PiBot)

Stepper Forearm
190 Ncm, 1.4A

Rotary Encoder
ASM 5048

Stepper Ellbow
26 Ncm, 0,4A

Rotary Encoder
ASM 5048

current pose

Webserver

Stepper Wrist
40 Ncm, 0.4A

Rotary Encoder
ASM 5048

trajectories

Servo Hand
DRS 101

9V 1A

I²C

9V 1A

Servo Gripper
DRS 101

Bot Mechanics

Bot Electronics

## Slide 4

Trajectory
Planning
visualization

Visual UI
Animation
openGL
Glut, GLUI

Trajectory Execution
Kinematics
(Webserver)

Trajectory Board
Odroid XU4
Linux C++

Angle Interpolation,
Motor and sensor control

Cortex Board
Arm Cortex M4 Realtime C++

Send Angle
via UART

Send PWM

Servo

Stepper

Send full trajectory of support points

Send joint angles at 10Hz

receive angle

Encoder

+

P

I

+

D

Control servos and encoders, compute speed profile and implement feedback-loop of actuators

Interpolate curve via bezier curve and compute kinematics

Define trajectory with support points

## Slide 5

Solution I:

Solution II:

ellbow

√((WCP_x ^2 + WCP_y ^2 ))

θ2

a

β

ellbow

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
WCPz-d0

c

θ1

√((WCP_x ^2 + WCP_y ^2 ))

γ

WCPz-d0

δ

δ

α

b

forward

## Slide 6

Computing support points of a cubic bezier curve

B‘

B

A‘

A‘ := A mirrored at B
B‘ := angle bisector of BA‘ and BC with length |BC|/3

A

C‘

C

D

y

y

top view

WCP

top view

WCP

ellbow

θ0

θ0

x

ellbow

x

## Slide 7

Walter‘s Cortex
ARM M4 (Teensy 3.5)
Realtime C++

closed loop runnig with 100 Hz

PID controller

Stepper
PWM generator
(AccelStepper)

to-be angles
and commands
at 10 Hz
via UART

to-be angles

PINs
- Direction
- Pulse
- Enable

Command Receiver

Herkulex Servo driver

Log / Uart

Magnetic Encoder
Reader

5x Pibot Stepper Drivers

HerkuleX
Protocol
Via UART

absolute angle via I²C

Bidirectional
Stepper with
4-wires

Servo

Magnetic
Encoder
ASM AS5048

Stepper

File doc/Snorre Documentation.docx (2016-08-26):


# Building a bad Robot

Jochen Alt

# 1 Architecture

In general, the data flow looks like this:


The visualizer is mainly the UI-based tool to plan trajectories by defining singular points. These points are sent to the Trajectory Execution, where the trajectory is interpolated using Bézier curves. Out of each point of the interpolated curve the angles are computed and send to the controller board, where a PID controller takes care that each actuator actually follows the curve.

On the mechanical side, we have two actuators driven by a servo (mainly due to space restrictions) and four actuators driven by a stepper/rotary encoder combination.

The servos (Herkulex DRS-101) are controlled directly by the controller board with an ATMega644 on board via a serial interface. The steppers do not have an internal feedback loop, so we need rotary encoders detecting the absolute angle of the joint and allowing to implement feedback controllers. Depending on the actuator, the steppers provide a torque between 26Ncm (turning the elbow) and 3,1Nm (upperarm). For space reasons, the gripper and the wrist is driven by a servo.


Figure 1-1 Architecture

The steppers are driven by retail stepper drivers (PiBot Stepper Driver) around the popular PWM stepper driver Toshiba 6600 (4.5A max). The stepper drivers are directly controlled via the Controller Board. It receives joint angles at a sample rate of 20Hz, interpolates in between, and sends the according PWM signal to the stepper drivers and to the servos.. Besides micro interpolation of the trajectory, the controller board takes care of the speed profile, i.e. it limits the acceleration and speed of each actuator. The controller board is a DIY board around an ATMega 644 (for the sheer number of pins) running firmware in low level C++ on base of the Arduino library.

The controller board is fed by the trajectory board, which is an octa core board (Odroid XU4).

The trajectory controller board is encapsulated by a webserver exposing the current movement and accepting commands like new trajectories.

# 2 Trajectories

Planning a trajectory means defining a sequence of poses in 3D space. These defined poses are interpolated in order to result in a smooth and continuous curve. Most beautiful are cubic Bézier curves for that purpose.

Bézier curves are polynoms of 3rd grade using a start and an end point and two support points defining the curvature at the start and end point. The computation is done on base of a parameter t=0..1 defining the ratio of the current position and four points P0..P3, of which P1 and P2 are support points the curve does not touch.

C_(bezier) (t)= ∑_0^3 (3i)t^i (1-t)^(3-i) P_i = (1-t)^3 P_0 +3t(1-t)^2 P_1 +3t^2 (1-t)P_1 + t^3 P_3 | (2-1)


This computation is done for x,y, and z coordinates. Normally being beautiful, but Bézier curves have a tendency to “bounce”, if the support points P1 and P2 differ too much in terms of the distance to the trajectory points P0 and P3. So, it is necessary to normalize support points by a small trick:

The picture illustrates a trajectory defined by A, B, C, and D. We want to model the piece between B and C with a cubic Bézier curve.

The support point B’ is computed by taking point A, mirroring it at B (A’), and moving along the angle bisector of A’ B C by a 3rd of the length of BC, C’ is computed in an analogous manner.

This approach is rather arbitrary, but results in a smooth and non-oscillating curve.

Having a nice trajectory, we need to convert the coordinates into angles of the joints. This is done by inverse kinematics in the following chapter.

# 3 Kinematics

Kinematics is about computation of the tool-centre-point (TCP) out of joint angles and vice versa. First is demonstrated in chapter 3.1 (simple), latter in chapter 3.2 (tricky).

But before starting any kinematics, it is necessary to define all coordinate systems.


Figure 3-1 Coordinate Systems in default position

The most important design decision is to let the three upper axis’ intersect in one point, the so-call wrist-center-point (WCP). This decision makes the computation of the inverse kinematic feasible.

The picture shows the used coordinate systems in the default position of the bot, having all angles at 0°, starting from the base (angle0) and ending with the coordinate system of the hand (angle6). For convenience the forearm (angle1) adds +90° to the real angle in order to have the base position at 0°of the bot, although the illustrated actually is -90°. The coordinate systems have been are arranged according to the Denavit Hardenberg convention, which is:

- The angle rotates along the z-axis
- The z-axis points on the direction of the next joint
- The transformation from anglei to anglei+1 is given via
1. rotating around the x-axis by α
2. translation along the x-axis by a
3. translation along the z-axis by d, and
4. rotation around the z-axis by joint angle θ

So, the Denavit Hardenberg parameters are:

Joint | a[°] | a[mm] | d[mm]
hip | -90° | 0 | d0
upperarm | 0 | a1 | 0
forearm | -90° | 0 | 0
ellbow | 90° | 0 | d3
wrist | -90° | 0 | 0
hand | 0 | 0 | d5

Table 3-1 Denavit Hardenberg parameters

The general definition of a Denavit Hardenberg transformation is

T=(cosθ, -sinθ, 0, a cosθsinθ, cosθ, 0, a sinθ0, sinα, cosα, d0, 0, 0, 1) | (3-1)

Combined with the DH parameters, the following DH matrixes define the transformation from one joint to its successor:

T_0^1 =(cosθ_0 , 0, -sinθ_0 , 0sinθ_0 , 0, cosθ_0 , 00, -1, 0, d_0 0, 0, 0, 1) | (3-2)
T_1^2 =(cosθ_1 , -sinθ_1 , 0, a_1 cosθ_1 sinθ_1 , cosθ_1 , 0, a_1 sinθ_1 0, 1, 0, 00, 0, 0, 1) | (3-3)
T_2^3 =(cosθ_2 , 0, -sinθ_2 , 0sinθ_2 , 0, cosθ_2 , 00, -1, 0, 00, 0, 0, 1) | (3-4)
T_3^4 =(cosθ_3 , 0, sinθ_3 , 0sinθ_3 , 0, -cosθ_3 , 00, 1, 0, d_3 0, 0, 0, 1) | (3-5)
T_4^5 =(cosθ_4 , 0, -sinθ_4 , 0sinθ_4 , 0, cosθ_4 , 00, -1, 0, 00, 0, 0, 1) | (3-6)
T_5^6 =(cosθ_5 , -sinθ_5 , 0, 0sinθ_5 , cosθ_5 , 0, 00, 0, 1, d_5 0, 0, 0, 1) | (3-7)

## 3.1 Forward Kinematics

With the DH transformation matrixes at hand, computation of the bot’s pose out of the joint angles is straight forward. The matrix representing the gripper’s pose T_0^6 is

T_0^6 = T_0^1 T_1^2 T_2^3 T_3^4 T_4^5 T_5^6 | (3-8

By multiplying the transformation matrix with the origin (as homogeneous vector), we get the absolute coordinates of the tool centre point in world coordinate system (i.e. relative to the bot’s base).

TCP= (, 000, 1)T_0^6 | (3-9)

The orientation in terms of roll/nick/yaw of the tool centre point can be derived out of T_0^6 by taking the part representing the rotation matrix ( R_0^6 ). [^1]

R_0^6 = T_0^6 (, 111, 0) | (3-10)
yaw= α=atan2(R_0^6 _21 ,R_0^6 _11 ) | (3-11)
nick = β=atan2(-R_0^6 _31 ,√(R_0^6 _21 ^2 + R_0^6 _21 ^2)) | (3-12)
roll = γ=atan2(R_0^6 _32 ,R_0^6 _33 ) | (3-13)

Due to singularities, we need to consider β=π/2 and use

α=0 | (3-14)
γ=atan2(R_0^6 _12 ,R_0^6 _22 ) | (3-15)

instead. if β=-π/2

α=0 | (3-16)
γ=-atan2(R_0^6 _12 ,R_0^6 _22 ) | (3-17)

Note: Unfortunately, the gripper’s coordinate system is not appropriate for human interaction, since the default position as illustrated in Figure 3-1 is not nick/roll/yaw=(0,0,0). So, it is handy to rotate the gripper matrix such that the default position becomes (0, 0, 0) . The according rotation matrix represents a rotation of -90° along x,y, and z, which results in a simple rotation matrix of

T_6^7 = (0, 0, 1, 00, -1, 0, 01, 0, 0, 00, 0, 0, 1) | (3-18)

In the following, this is not considered, but we stop at the coordinate system T_5^6 to simplify the computation.

## 3.2 Inverse Kinematics

Inverse kinematics denotes the computation of all joint angles out of the tool-centre-point’s position and orientation. In general it is hard to give non-numeric solution, in this case it is possible since the upper three joint angles point to one point, the so-called wrist centre point (Figure 1-1).

We know the TCP’s position and orientation in terms of roll, nick, yaw ( γ,β, α) .

TCP_(position) = (tcp_x tcp_y tcp_z 1) TCP_(orientation) = (tcp_γ tcp_β tcp_α 1) | | | (3-19

First, we need to compute the wrist-centre-point out the tool-centre-point. This is possible by taking the TCP and moving it back along the TCP’s orientation by the hand length. For doing so, we need the transformation matrix from the base to the last joint T_0^6 , which we can derive out of the TCP’s position and orientation.

To build the transformation matrix T_0^6 we need the rotation matrix defining the orientation of the tool-centre-point. This is given by multiplying the rotation matrixes for all axis (γ,β, α) which gives R= R_y R_β R_α

R_0^6 = (cosβcosγ , -cosβsinγ , -sinβ-sin αsinβcosγ+cosαsinγ , sinαsinβsinγ+cos αcosγ, -sinαcosβcosαsinβcosγ+sinαsinγ , -cosαsinβsinγ+sinαcosγ, cosαcosβ) | (3-20)

Now we can denote the transformation matrix of the TCP

T_0^6 = (cosβcosγ , -cosβsinγ , -sinβ, tcp_x -sin αsinβcosγ+cosαsinγ , sinαsinβsinγ+cos αcosγ, -sinαcosβ, tcp_y cosαsinβcosγ+sinαsinγ , -cosαsinβsinγ+sinαcosγ, cosαcosβ, tcp_z 0, 0, 0, 1) | (3-21)

From the TCP’s perspective, WCP is just

WCP_(TCP) =(00-d_5 1) = | (3-22)

Furthermore, WCP=TCP+ WCP_(TCP) = T_0^6 WCP_(TCP) , so we get the wrist-centre-point by

WCP = T_0^6 (00-d_5 1) | (3-23)

in world coordinates. Having a top view on the robot shows how to compute the first angle:


Figure 3-2 Two solutions for θ_0 viewed from above

θ_(0,1) =atan2(WCP_x ;WCP_y ) | (3-24)

Actually, this angle exists in two variants: if the bot looks backwards, another valid solution is

θ_(0,2) =atan2(-WCP_x ;-WCP_y ) | (3-25)


Thanks to the design having a wrist-centre-point where the axes of the three upper actuators intersect, the next two angles can be computed by a triangle:

Figure 3-3 Triangle to compute θ_1 and θ_2

Again, there are two solutions representing, one configuration corresponds with a natural pose of the elbow, solution II is a rather unhealthy position:


Figure 3-4 computing θ_1 and θ_2 with the cosine sentence

a and b is given by the length of the actuators a1 und d3 (Table 3-1). So, cosine sentence yields the angles α and γ .

α= cos^(-1) ((a^2 -b^2 -c^2)/(-2bc)) | (3-26)
c^2 =a^2 +b^2 -2ab cosγγ=cos^(-1) ((c^2 -a^2 -b^2)/(-2ab)) | (3-27)

Finally, we the get

θ_(1,1) =π/2-(γ+ a) | (3-28)
θ_(2,1) =π/2-γ | (3-29)

and – as second solution -

θ_(1,2) =π/2-(γ-a) | (3-30)
θ_(2,2) =3π/2-γ | (3-31)

The upper angles θ3, θ4, θ5 can be obtained by considering by the chain of transformation matrixes. With

T_0^6 = T_0^3 T_3^4 T_4^5 T_5^6 = T_0^3 T_3^6 | (3-32)

we get

T_3^6 = T_3^4 T_4^5 T_5^6 = (T_0^3 )^(-1) T_0^6 | (3-33)

Although the need of the annoying multiplication T_3^4 T_4^5 T_5^6 out of (3-5), (3-6), and (3-7) we only need to consider the rotation part of the homogenous matrixes, since just the orientation of the tool-centre-point is relevant here.

R_3^6 =R_3^4 R_4^5 R_5^6 =(cosθ_3 cosθ_4 cosθ_4 -sinθ_3 sinθ_5 , -cosθ_3 cosθ_4 sinθ_5 -sinθ_3 cosθ_5 , -cosθ_3 sinθ_4 sinθ_3 cosθ_4 cosθ_5 +cosθ_3 sinθ_5 , -sinθ_3 cosθ_4 sinθ_5 +cosθ_3 cosθ_5 , -sinθ_3 sinθ_4 sinθ_4 cosθ_5 , -sinθ_4 sinθ_5 , cosθ_4 ) | (3-34)

T_0^6 - and therefore the rotation part - R_0^6 is already known by (3-21).

(T_0^3 )^(-1) resp. (R_0^3 )^(-1) can be obtained out of the given angles θ0,θ1,θ2 by

(R_3^6 )= (R_0^1 R_1^2 R_2^3 )^(-1) R_0^6 | (3-35)

So, by equalizing the values of matrix R_3^6 with (3-35) we get θ4 :

cosθ_4 =(R_3^6 )_33 | (3-36)

having two solutions

θ_(4,1/2) =±arccos(R_3^6 )_33 | (3-37)

For θ4 there is no easy matrix element, but we can combine

-sinθ_3 sinθ_4 =(R_3^6 )_23 | (3-38)
-cosθ_3 sinθ_4 =(R_3^6 )_13 | (3-39)

to

tanθ_3 =((-(R_3^6 )_23)/(sinθ_4))/(((R_3^6 )_13)/(sinθ_4)) | (3-40)

which ends up in

θ_3 =atan2((-(R_3^6 )_23)/(sinθ_4), ((R_3^6 )_13)/(sinθ_4) ) | (3-41)

again having two solutions depending on θ4 . Same is done on θ5:

θ_5 =atan2(((R_3^6 )_32)/(sinθ_4), -((R_3^6 )_31)/(sinθ_4) ) | (3-42)

If θ4=0, we have an infinite number of solutions θ3 and θ5 (gimbal lock). In that case, we consider (R_3^6 )_12

(R_3^6 )_12 = -(cosθ_3 sinθ_5 +sinθ_3 cosθ_5 ) | (3-43)

since we know the trigonometric addition theorem from school

(cosθ_3 sinθ_5 +sinθ_3 cosθ_5 )= sin⁡(θ_3 + θ_5 ) | (3-44)

we get

(R_3^6 )_12 = -(cosθ_3 sinθ_5 +sinθ_3 cosθ_5 ) = - sin⁡(θ_3 + θ_5 ) | (3-45)

We are free to choose θ_3 and take the bot’s current angle θ_3 to not move unnecessarily.

θ_5 =asin(-(R_3^6 )_12 )- θ_3 | (3-46)

In the end, we get eight solutions by combining the possible pose configurations of θ_0 (forward/backward), θ_1 and θ_2 (triangle flip), and θ_4 (hand orientation turn).

The “right” solution is chosen by taking the one that differs the least from the current bot’s joint angles.

# 4 Trajectory Execution

Now we have the trajectory in terms of a sequence of joint angles. This needs to be translated into movements of the motors. This translation should be done in a manner that no motors limits are violated, and with a speed profile that avoids vibrations. Typically, this is done with speed profile of constant acceleration. I.e. if the required acceleration is higher than an upper limit, the speed is increased with a limited acceleration until the to-be speed is reached.

Additionally, we need to control a feedback loop to ensure that the to-be angle of the motor is actually reached.

All this is done in the controller board. It receiving the joint angles at 20Hz and the angles of the magnetic encoders, and let that control with a PI controller producing the PWM signal for the steppers.


Figure 4-1 Components of the Controller Board

The software runs on the basis of the Arduino library

Besides software, this requires just a few components, it is mainly an 8-bit ATMega 644 overclocked at 24 MHz[^2].


Figure 4-2 Schematics of the controller board

Most parts of the layout are for the power supply at the bottom. The µC gets 5V by a 7805, the two servos are driven by a 7809 providing 2A. Additionally, there are two relays for a proper start-up procedure switching the 240W power supply for the steppers and the power supply for the servos. This has been necessary to avoid impulses to the motors inducing annoying ticks when power is switched on. So, after booting the Trajectory Board and switching on the Controller Board, the controller board disables all stepper drivers, then turns on the stepper power supply, then turns on the servos power supply. By that procedure, no ticks are happening then starting up.

On the top there is the ATMega controller with an integrated-oscillator (to ensure a properly running software-based UART) and lots of sockets for the stepper drivers, encoders and servos. All this fits on a small PCB:


Figure 4-3 Layout of the controller board

# 5 References

1. Controller board schematics ./schematics/BotController.sch created with KiCad
2. Controller board layout ./schematics/BotController.kicad-pcb

[^1] https://de.wikipedia.org/wiki/Roll-Nick-Gier-Winkel#Berechnung_aus_Rotationsmatrix
[^2] I regard overclocking of self-made PCBs as an obligation

Jochen Alt 14

SNORRE a feminist robot

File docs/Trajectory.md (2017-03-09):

Planning a trajectory means defining a sequence of poses in 3D space. These defined poses are interpolated in order to result in a smooth and continuous curve. Most beautiful are cubic Bézier curves.

Bézier curves are polynoms of 3<sup>rd</sup> grade using a start and an end point and two support points defining the curvature at the start and end point. The trajectory is defined by the start and the end point, the support point is not on the trajectory but used to make it smooth only. The computation is based on a parameter *t=0..1* defining the ratio of how much the current position has already made of the full curve. Let’s assume, we have the four points *P<sub>0</sub>..P<Sub>3</sub>*, of which *P<sub>1</sub>* and *P<sub>2</sub>* are support points the curve does not touch:

&nbsp;&nbsp;&nbsp;&nbsp; 

This computation is done for *x*, *y*, and *z* coordinates. Although being beautiful, Bézier curves have a tendency to “bounce”, if the support points *P<sub>1</sub>* and *P<sub>2</sub>* differ too much in terms of the distance to the trajectory points *P<sub>0</sub>* and *P<sub>3</sub>*. So, it is necessary to normalize support points by a small trick:

The picture illustrates a trajectory defined by *A*, *B*, *C*, and *D*. We want to model the piece between *B* and *C* with a cubic Bézier curve.



The support point *B’* is computed by taking point *A*, mirroring it at *B* (*A’*), and moving along the angle bisector of *A’* *B* *C* by a 1/3 of the length of *BC*, *C’* is computed in an analogous manner.

This approach is rather arbitrary, but results in a smooth and non-oscillating curve. On the left, we see a linear trajectory, on the right the same curve as bezier curve. All this is implemented in [BezierCurve.cpp](https://github.com/jochenalt/Walter/blob/master/code/WalterKinematics/src/BezierCurve.cpp).




Now the curve looks fine, but simply following that curve is not enough to make a smooth movement. We need a speed profile that avoids jerky movements. This is done by speed profiles. The classical approach is to use trapezoidal speed profiles like this:




This trapezoid speed profile results in a constant (maximum) acceleration, then continuing with no acceleration, and a constant deceleration until zero speed is reached. To get the position on a curve, speed is integrated over time 

Despite of the corners in the speed profile, the position profile looks smooth. Still, how is a profile like that computed? Having a constant acceleration *a*, start speed v<sub>start</sub>, an end speed v<sub>end</sub>, the distance *d* (length of the Bezier curve) and the desired duration of the complete profile *t<sub>g</sub>*, we need to compute the time *t<sub>0</sub>* and *t<sub>1</sub>* which is the duration of the starting acceleration and final deceleration. The full distance is given by

&nbsp;&nbsp;&nbsp;&nbsp;

The duration and speed of the plateau is given by 

&nbsp;&nbsp;&nbsp;&nbsp;
&nbsp;&nbsp;&nbsp;&nbsp;

Rearranging these equations to get *t<sub>0</sub>* ends up in

&nbsp;&nbsp;&nbsp;&nbsp;

with

&nbsp;&nbsp;&nbsp;&nbsp;
	
Finally, with the equation above we get

&nbsp;&nbsp;&nbsp;&nbsp;
	
With the equation above on computing *d* we get *t<sub>g</sub>*.

This holds true for a trapezoid profile only, since to model a full trajectory that consist of single movements we also need profiles that represent a ramp or stairways, depending on the constrains in terms of duration, distance, and start/end speed. This ended up in quite a lot of code treating all the different cases. 

On the right, the effect of a speed profile is illustrated compared to the same trajectory without speed profile. The effect is not spectacular, but can be detected when watching the top left and bottom left corner: On the left, the movement is continous. On the right, the movement stops slowly and accelerates when it continues.Speed profiles are implemented in [SpeedProfile.cpp](https://github.com/jochenalt/Walter/blob/master/code/WalterKinematics/src/SpeedProfile.cpp).




All this is done while planning a trajectory, so it is done upfront. At runtime, the trajectory is fully compiled and contains bezier curves and speed profiles already. The according UI where trajectories are planned looks like this (source code is [WalterPlanner](https://github.com/jochenalt/Walter/blob/master/code/WalterPlanner))



This UI provides forward and inverse kinematics (explained in [Kinematics](./Kinematics)), allows to define a trajectory by defining support points (indicated by big green balls). After having assigned some parameters like speed or duration the trajectory is compiled, i.e. the bezier curves and speed profiles are computed (indicated by small green balls). This trajectory can be send to Walter to be executed by its Cortex. 

Now we have a nice trajectory with a smooth speed profile, but do not yet know how to compute the angles of the joints. 

This is explained in [Kinematics](./Kinematics) and will be tough to read, take your time.

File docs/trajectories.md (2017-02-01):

Planning a trajectory means defining a sequence of poses in 3D space. These defined poses are interpolated in order to result in a smooth and continuous curve. Most beautiful are cubic Bézier curves.

Bézier curves are polynoms of 3rd grade using a start and an end point and two support points defining the curvature at the start and end point. The trajectory is defined by the start and the end point, the support point is not on the trajectory but used to make it smooth only. The computation is based on a parameter t=0..1 defining the ratio of how much the current position has already made of the full curve. Let’s assume, we have the four points P0..P3, of which P1 and P2 are support points the curve does not touch.

 

This computation is done for x, y, and z coordinates. Normally being beautiful, but Bézier curves have a tendency to “bounce”, if the support points *P<sub>1</sub>* and *P<sub>2</sub>* differ too much in terms of the distance to the trajectory points *P<sub>0</sub>* and *P<sub>3</sub>*. So, it is necessary to normalize support points by a small trick:

The picture illustrates a trajectory defined by A, B, C, and D. We want to model the piece between B and C with a cubic Bézier curve.



The support point B’ is computed by taking point A, mirroring it at B (A’), and moving along the angle bisector of A’ B C by a 3rd of the length of BC, C’ is computed in an analogous manner.

This approach is rather arbitrary, but results in a smooth and non-oscillating curve.

Now the curve looks fine, but simply following that curve is not enough to make a smooth movement. We need a speed profile that avoids jerky movements.

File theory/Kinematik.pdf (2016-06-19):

3. Kinematisches Modell

und die Parameteridentifikation diskutiert.; Industrieroboter bestehen aus mehreren, durch Gelenke miteinander verbundene Teilstrukturen. Bei der Beschreibung ihres stationären Positionierverhaltens wird ein starres Mehrkörpersystem zugrunde gelegt. Die regulär nummerierten G Teilkörper; sind; dabei; ebenfalls; durch; regulär; nummerierte G Gelenke, die Drehachsen; und; Führungen; des; Industrieroboters,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

13.05.2013 V3.4 | - 3-1 - | © Dr-Ing. habil. Jörg Wollnack

## 3 Kinematisches Modell

Im Folgenden werden die mathematischen Ansätze zur Beschreibung offener, unverzweigter kinematischer Ketten eingeführt, die zur Modellierung des stationären Positionierverhaltens des Roboters dienen. Auf der Basis der homogenen Transformationen werden die Koordinatentransformationen der kinematischen Kette des Industrieroboters definiert. Die bekannten und in der Robotik etablierten Transformationstypen werden hinsichtlich ihrer Eignung untersucht und bewertet. Zur Beschreibung des Fehlerfortpflanzungsverhaltens der kinematischen Kette wird eine neue analytische Methode entwickelt, die die rekursive analytische Beschreibung der verallgemeinerten Taylorschen Reihe des kinematischen Modells zulässt. Es wird kurz der Begriff der inversen kinematischen Transformation eingeführt, werden Verfahren zur Berechnung mit ihren Querverbindungen zur analytischen Differenziation aufgezeigt, das Beschleunigungs- Kraft- sowie Momentenverhalten erörtert, die internen Sensorgleichungen beschrieben, Verfahren zur Werkzeug- und Montageposebestimmung aufgezeigt

lung des Industrieroboters wird allein durch die rotatorischen Gelenke bestimmt. Die Position des Industrieroboters wird jedoch sowohl von den Rotationsachsen als auch von den Translationsachsen beeinflusst. Gewöhnlich werden hierbei kartesische Koordinatensysteme verwendet.

Im Raum hat ein beweglicher, starrer Körper sechs Freiheitsgrade f = 6, die in einem kartesischen Bezugskoordinatensystem durch drei Rotations- und drei Translationsparameter beschrieben werden. Ein einzelnes Gelenk eines Industrieroboters kann wegen der mechanischen Kopplung maximal fünf der existierenden sechs Freiheitsgrade nutzen, so dass der Antriebsfreiheitsgrad fAi des i-ten Gelenks im Intervall

0 f | f Ai
(f = 5) | (3-1)

liegt. Typischerweise werden die Gelenke nur mit einem Gelenkfreiheitsgrad "eins" als Drehoder Schubgelenke ausgeführt.

Abb. 3-1: Schema der offenen kinematischen Kette

13.05.2013 V3.4 | - 3-2 - | © Dr-Ing. habil. Jörg Wollnack

Die Anzahl der Bewegungsachsen des Industrieroboters oder der Getriebefreiheitsgrad

f | f
i
| i
B | A
Glieder

(3-2)

der offenen kinematischen Kette muss nicht identisch mit dem Freiheitsgrad f sein. Dennoch kann der Freiheitsgrad fK des Endeffektorkoordinatensystems gegenüber dem Bezugs- oder Weltkoordinatensystem S⁰
die maximale Anzahl der Freiheitsgrade f nicht überschreiten, so dass die Relation

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
f | f | f | f
f | f
| K | | | | | B
K | B

für
sonst

(3-3)

gilt. Ist der Getriebefreiheitsgrad größer als 6 ( fB > f ), so kann die erhöhte "Beweglichkeit" des Industrieroboters dazu genutzt werden, z.B. um Hindernisse herumzugreifen.

Bei dem üblicherweise realisierten Aufbau eines Industrieroboters mit nur einem Freiheitsgrad hinsichtlich der Translation oder¹ Rotation lassen sich die Transformationen der Achskoordinaten des Industrieroboters in ein Weltkoordinatensystem S

0
in mehrere Elementartransformationen zerlegen. Aus dieser roboterspezifischen Zerlegung ergeben sich die typischen Grundformen von Robotern und Arbeitsraumbeschreibungen. Die Aufgabe der kinematischen Transformation besteht darin, die Endeffektorposition und -orientierung, die allgemein als Pose bezeichnet wird, im Welt- oder Roboterkoordinatensystem zu berechnen. Hierzu werden typischerweise körperfeste, lokale kartesische Koordinatensysteme in die Bewegungsachsen des Industrieroboters gelegt, so dass hierdurch eine Kette von lokalen Koordinatensystemen und Transformationen entsteht. Die rekursive Transformationsvorschrift Ti-1

ergibt sich in
homogen Koordinaten
t | 4
ri | i | i | i x | y | z | kM

(3-4)

zu:

1 | 1 | 1 : T | r | T r i | i | i | i

,

1 | 1 | 44
1
M
i | i | x
i
k

D t
T
0

, i {1,...,G}
, mit | (3-5)

i

r

:= Ortsvektor im i-ten Koordinatensystem,
t
i 1

:= Translationsvektor zwischen dem (i-1)-ten und i-ten Koordinatensystem im (i-1)-ten Koordinatensystem beschrieben,

Di 1

:= Rotationsmatrix der absteigenden Koordinatentransformation und
kM
:= Skalierungsfaktor . | (3-6)

Der Faktor kM ermöglicht eine Gesamtskalierung, die bei einer maßstabsgetreuen Darstellung, wie sie in der Robotik erforderlich ist, zu kM = 1 zu setzen ist. Zwischen den neun Richtungskosinussen, die eine Drehung charakterisieren, existieren wegen der Orthogonalitätsrelation

Di Di E

t
(3-7)

nur sechs unabhängige Gleichungen, weshalb die Drehung allein mit drei Größen und die homogene Transformationsmatrix mit sechs Parametern eindeutig beschreibbar ist. Bei der homogenen Koordinatentransformation handelt es sich um eine eindeutige Abbildung.

1 Unter dem sprachlichen ´oder´ soll hier das logische ´exklusiv-oder´ verstanden sein.

13.05.2013 V3.4 | - 3-3 - | © Dr-Ing. habil. Jörg Wollnack

Die bei der sukzessiven Koordinatentransformation entstehende resultierende Koordinatentransformation kann aufgrund der homogenen Koordinaten über den Produktterm

T Tj

j {q,q 1,...,G 1}

, q {0,1,2,...,G 2}

(3-8)

beschrieben werden. Diese Matrix stellt die kinematische Transformation dar, wobei q den Index des Roboter- oder des Bezugskoordinatensystems angibt.

Die
Tj

-Matrizen der kinematischen Transformation sind von den entsprechenden Transformationsparametern des Gelenkübergangs abhängig. Je nachdem, welche Beschreibungsform für diese Gelenkübergänge gewählt wird, hängt jede Matrix von einer bestimmten Anzahl von Parametern ab. Dabei sind gewisse Parameter konstant und andere Variable, so dass eine Abbildung im Sinne von

t | t | t ' | ' | t | t | t | t ( ) | ( , ) , mit | , | , | und T T p | T p x | p | p x | p | p | x | x i | i

'
( ) | ( , ) T | T p | T p x j | j | j | j | j | j
. | (3-9)

vorliegt.

Die Aufgabe der inversen kinematischen Transformation ist es, unter vorgegebener Pose die Gelenkstellungen der homogenen Transformationsmatrizen zu berechnen. Die inverse kinematische Transformation ist nicht notwendigerweise eindeutig, so dass für eine Pose mehrere Lösungen existieren können. Ferner sind für den allgemeinen Fall bisher keine analytischen Lösungen bekannt. Für weitere Einzelheiten zur inversen kinematischen Transformation sei auf Kap. 3.4 verwiesen.

## 3.1 Allgemeine Ansätze

Bisher wurde bewusst offen gelassen, wie die Rotations- und Translationsparameter der Gelenkkoordinatentransformationen in Zusammenhang mit den konstruktiven Größen eines Roboters stehen. Diese Beschreibungen lassen sich nicht für die Charakterisierung der Kinetik heranziehen, da hierfür die Ortskoordinaten der Teilkörperschwerpunkte und nicht die Ortskoordinaten der Gelenke benötigt werden.

Prinzipiell gibt es eine Reihe von Beschreibungsformen, die sich hinsichtlich der Transformationsparameter und ihren Eigenschaften unterscheiden, z.B.:

Roll-Pitch-Yaw-Transformation [107], Euler-Transformation,
Denavit-Hartenberg-Transformation [23], Hayati-Mirmirani-Transformation [53], Veitschegger-Wu-Transformation [158] usw.

Die Wahl einer bestimmten Transformation wird in der Regel von Anwendungs- oder Anschaulichkeitsaspekten geleitet, auf die im Folgenden kurz eingegangen werden soll.

Roll-Pitch-Yaw- und Elementartransformationen; Die; 6-dimensionale; Roll-Pitch-Yaw-; Transformation (RPY); besitzt; drei; Transformationsbeziehungen zweier karte- sischer Koordinatensysteme verwenden, weshalb sie häufig zur Charakterisierung von Posen herangezogen wird.; Die homogene Transformationsmatrix (3-5); mentare; Translations-; und; Rotations-; ( +1)-tes Gelenk; i-tes Gelenk

13.05.2013 V3.4 | - 3-4 - | © Dr-Ing. habil. Jörg Wollnack

Minimalität der kinematischen Transformation

Die kinematische Transformation der offenen und unverzweigten kinematischen Kette, deren Elemente durch Dreh- und Schubgelenke verbunden sind, ist minimal und vollständig, wenn sie genau

n | r | t K | 4 K | 2 K | 6

(3-10)

Parameter enthält [135], wobei rK die Anzahl der Drehgelenke und tK die Anzahl der Schubgelenke angibt. Dies macht deutlich, dass bei Rotationsgelenken 4 parametrige und bei Translationsgelenken 2 parametrige Achsmodelle zur Konstruktion minimaler Systeme hilfreich wären. Die Zielsetzung der Konstruktion minimaler Modelle hat dabei zu verschiedenen Konventionen bei der Beschreibung benachbarter Achsbeziehungen geführt. Dabei wurde der Gewinn an Minimalität zumeist durch den Verlust an Eindeutigkeit und einer Zunahme von Rangdefekten erkauft.

Positions- und drei Rotationsparameter tx, ty und tz sowie x, y und z (siehe Abb. 3-2). Sie lässt sich zur Beschreibung beliebiger

der RPY-Transformation lässt sich über ele-

operationen beschreiben, die nur von einem Transformationsparameter abhängig sind:

T T
z | z
Ty | y | Tx | x | TRz | z
TRy | y | TRx | x
(t ) | (t ) | (t ) | ( | ) | ( | ) | ( | )
, mit | (3-11)

Translation

t
3

00 ()
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
0 0 ()

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
00 ()
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
, (3-12)

Rotation

( | ) ( | )
1
x | x
Rx | x

R 0 T
0

,

( | ) ( | )
1
y | y
Ry | y

R 0 T
0

,

,

( | ) ( | )
1
z | z
Rz | z

R 0 T
0
, mit | (3-13)

Abb. 3-2: Koordinatentransformation zwischen benachbarten Gelenken

13.05.2013 V3.4 | - 3-5 - | © Dr-Ing. habil. Jörg Wollnack Rx | x | x | x
x | x
( | ) | cos | sin
| | sin | cos

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
1 | 0 | 0
0
0
, R y | y
y | y
y | y
( | )
cos | sin
sin | cos

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
0 | 1 | 0
| 0

,

R
z | z
z | z
z | z
( | )
cos | sin
sin | cos

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
0 | | 0 | | 1
und | (3-14)
D D( ) R ( | ) R ( | ) R ( | )
z | z | y | y | x | x
. | (3-15)

Die homogene Transformationsmatrix
Tj T

der j-ten Transformation des Produktterms (3-8)

Tj T p j

( ' )

(3-16)

ist eine Funktion des Transformationsparametervektors

p' | t , | ( | , | , | , | , | , | ) j | j | j | x j | y j | z j | x j | y j | z j
t | t | t
t | t

t
t
e | j
. | (3-17)

Der im 3. Kap. eingeführte Begriff der Pose zwischen zwei Koordinatensystemen lässt sich nach der Wahl einer bestimmten Koordinatentransformation als Zahlentupel

6
' p j

der
Transformationsparameter dieser Transformation definieren². Für die RPY-Transformation berechnet sich die Pose aus der homogenen Transformationsmatrix zu:
t | p | T

t
;

t

( ) c 1 2 h
t

RPY

, mit

t | t | t | t
14 | 24 | 34 b | g
t
,
1;2 | x1;2 | y1;2 | z1;2

t

d | i ,

y1;2

R
S
T

arcsin( )
arcsin( )

t
t

31

31

für I. und II. Quadranten
für III. und IV. Quadranten

,

x1;2

arctan ( | / cos( | ) , | / cos( | )) 2 32 | 1;2 | 33 | 1;2
t | t
y | y

für
y1 2

0
; 90

und

z1;2

arctan ( | / cos( | ) , | / cos( | )) 2 21 | 1;2 | 11 | 1;2
t | t
y | y

für
y1 2

0
; | 90 . | (3-18)

Es existieren grundsätzlich zwei Posevektoren, die die Matrix T beschreiben. Durch die Beschränkung auf die RPY-Hauptwerte
y

[ 0, ]

, lässt sich die Eindeutigkeit der Poseberechnung sicherstellen.

Translatorische Bewegungen können bei der RPY-Transformation in Richtung des Ortsvektors
t t

oder in Richtung einer der Einheitsvektoren e , {x, y,z}

beschrieben
werden und rotatorische Bewegungen repräsentieren Drehungen um eine der Koordinatenachsen
, {x, y,z}

. Damit lässt sich diese Transformation sowohl für Schub- als auch Drehgelenke verwenden.

2 Konsequenterweise müßte der Posevektor mit der verwendeten Transformation indiziert werden, da nur unter ihrer Kenntnis der Begriff der Pose Sinn hat. Auf die Indizierung wird jedoch in der Regel verzichtet.

Gelenk +1 i; Glied +1 i; Glied -2i; Gelenk -1i; Gelenk i; Glied -1i; Glied i; Roos

13.05.2013 V3.4 | - 3-6 - | © Dr-Ing. habil. Jörg Wollnack

Der Vorteil der RPY-Transformation liegt in dem isolierten, nur punktförmigen Rangverlust. Ihr Nachteil beruht auf dem 6 parametrigen Transformationstyp, der bei der Beschreibung von Kinematiken zum Minimalitätsverlust führt (siehe Tab. 3-1).

Denavit-Hartenberg-Transformation

Die Denavit-Hartenberg-Transformation (DH), siehe Abb. 3-3, erlaubt die Beschreibung be-

liebiger mechanischer Gelenke mit nur vier Parametern. Die geringe Anzahl der Parameter ergibt sich aus der Einschränkung der Freiheitsgrade benachbarter Koordinatensysteme. Das Modell ist sowohl für Dreh- als auch Schubgelenke geeignet.

3 Um eine kompakte Schreibweise zu ermöglichen, steht c für cosinus und s für sinus.

Transformationstyp | T ( ) x T y ( ) t y T z ( ) t z T Rz ( z ) T Ry ( y ) T t Rx ( x T ) x

Transformation

Rangverlust | Ist identisch mit dem Rangverlust des Rotationsteils und tritt bei Drehungen auf, bei der die z-Achse in die x/y-Ebene übergeht ( y 90⁰ ).
Vollständigkeit | ja (global)
Stetigkeit | ja
Minimalität | 6 parametrig

Tab. 3-1: Eigenschaften der RPY-Transformation

Abb. 3-3: Denavit-Hartenberg-Transformation

Transformation; Rangverlust; bei parallelen Achsen; Vollständigkeit; ja (global); Stetigkeit
Gelenk +1 i; Gelenk i; Roos

13.05.2013 V3.4 | - 3-7 - | © Dr-Ing. habil. Jörg Wollnack
Transformationstyp | T R ( ) T ( ) T ( ) a R d ( ) z z x x
Minimalität | 4 parametrig

Tab. 3-2: Eigenschaften der Denavit-Hartenberg-Transformation

Der Vorteil der DH-Transformation liegt in ihrem 4 parametrigem minimalen Ansatz. Von Nachteil ist, dass bei parallelen Achsen ein Rangverlust auftritt (siehe Tab. 3-2).

Dieser Rangverlust ist problematisch, da aufgrund der stets vorhandenen Fertigungsfehler, Messfehler und Toleranzen die Sollwerte der Konstruktionsparameter eines Industrieroboters nicht exakt einzuhalten sind. Bei aufeinanderfolgenden, fast parallelen Achsen ist die DH-Transformation aufgrund des Rangverlustes und der o.g. Fehler schlecht konditioniert, womit hinsichtlich der Fehlerfortpflanzung ein ungünstiges Verhalten entsteht [11, 98]. Im Hinblick auf die Verbesserung der Positioniergenauigkeit von Industrierobotern mittels Roboterparameteridentifikation gilt es gerade, diese individuellen Roboterparameter zu identifizieren, und da die in der Montagetechnik bewährten Horizontal-Knickarm-Roboter (SCARA) nahezu parallele Drehachsen aufweisen, ist die Verwendung der DH-Transformation für die Genauigkeitssteigerung einer off-line-programmierbaren flexiblen Montagezelle nicht geeignet.

Hayati-Mirmirani-Transformation

Die Hayati-Mirmirani-Transformation (HM) in Abb. 3-4 stellt eine Erweiterung des DH-Modells dar, mit dem Ziel, den Rangverlust bei parallelen Achsen auszuschließen. Dies wird

durch eine zusätzliche Drehung um die y-Achse zusammen mit einer einparametrigen

Abb. 3-4: Hayati-Mirmirani-Transformation


13.05.2013 V3.4 | - 3-8 - | © Dr-Ing. habil. Jörg Wollnack

Beschreibung des Koordinatensystemursprungs erreicht. Das Modell ist nur für Drehgelenke geeignet und muss zur Anwendung auf Schubgelenke entsprechend modifiziert werden.

Transformationstyp | (nur Drehgelenke) T R T ' ( ) R ' ( ) R a '' ( ) ( ) z x x y

Transformation

Rangverlust | Bei orthogonalen Rotationsachsen und beliebigen Rotationsachsen, die sich im Ursprung des Ausgangskoordinatensystems schneiden.
Vollständigkeit | nein (global); nur lokal, für nicht aufeinanderfolgende identische Rotationsachsen
Stetigkeit | ja
Minimalität | 4 parametrig

Tab. 3-3: Eigenschaften der Hayati-Mirmirani-Transformation

Veitschegger-Wu-Transformation

Das von Veitschegger und Wu (VWU) entwickelte Modell kombiniert die DH- und HM-Ansätze mit dem Ziel, die Rangverluste für aufeinanderfolgende identische Achsen auszuschließen. Dies wird durch die Einführung eines weiteren Drehwinkels mit dem Verlust an Minimalität erreicht (siehe auch Abb. 3-4).

Transformationstyp | T R ( ) T z d Tx a Rx ( ) ( ) ( ) R y ( ) z ' ' ''

Transformation

Rangverlust | Bei Rotationsachsen, die die z-Achse im Ausgangskoordinatensystem schneiden und bei Rotationsachsen, die parallel zur x/y-Ebene liegen.
Vollständigkeit | ja (global)
Stetigkeit | ja
Minimalität | 5 parametrig

T

Tab. 3-4: Eigenschaften der Veitschegger-Wu-Transformation

Zusammenfassung

Die o.g. Transformationen haben jeweils spezifische Vor- und Nachteile, so dass keinem dieser Ansätze generell der Vorzug zu geben wäre. Unter dem Gesichtspunkt der Minimalität des Modells haben die DH- und die HM-Transformation eine höhere Präferenz, wobei die DH-Transformation für aufeinanderfolgende, (quasi) orthogonale und die HM-Transformation für (quasi) parallele Achsen einzusetzen ist.

Unter den Aspekten der Vollständigkeit und des Rangdefekts wäre die RPY-Transformation vorzuziehen. Dies hätte jedoch den Verlust der Minimalität zur Folge, weshalb die RPY-Transformation bisher hauptsächlich zur Posebeschreibung herangezogen wurde. Mit Hilfe des Verfahrens zur Konstruktion minimaler Modelle kann dieser Nachteil beseitigt werden. Damit lässt sich auch die RPY-Transformation für kinematische Modelle ohne Verlust der Minimalität einsetzen und man erhält ein vollständiges, minimales und hinsichtlich der


13.05.2013 V3.4 | - 3-9 - | © Dr-Ing. habil. Jörg Wollnack

Rangverluste vorteilhaftes Modell. Aus diesem Grunde wird im Folgenden nur die RPY-Transformation diskutiert.

## 3.2 Schnelle und exakte Differenziation

Ausgehend von der Produktform (3-8) erhält man mit der Produktregel die partielle Ableitung nach den Eingangsgrößen

'
{ | } k | xk | yk | zk | xk | yk | zk p | t t t

des parametrischen Modells zu [117]:

1 | 1
' | '
0 | 1
k | G
k
| j | j
p | p k | k k | j | j k

T
T | T | T , k | G {0,1,..., | 1} . | (3-19)

Da der Parameter nur in einer Transformation vorliegt, vereinfacht sich die Ableitung zu:

1 | 1
' | '
0 | 1
k | G
k
j | j
p | p k | k j | j k

T
T | T | T . | (3-20)

Zerlegt man den Term

' k
k

p

T (3-21)

in die Elementartransformationen (3-12) und (3-13), so erhält man

' | ' | ( ) | ( ) | ( ) | ( | ) | ( | ) | ( | ) k | z | zk | y | yk | x | xk | Rz | zk | Ry | yk | Rx | xk
k | k | t | t | t
p | p
T | T | T | T | T | T | T | (3-22)

bzw. nach erneuter Anwendung der Produktregel

' | ' | ( ) | ( ) | ( ) | ( | ) | ( | ) | ( | ) k | z | zk | y | yk | x | xk | Rz | zk | Ry | yk | Rx | xk
( ) | ( ) | ( ) | ( | ) | ( | ) | ( | ) z | zk | y | yk | x | xk | Rz | zk | Ry | yk | Rx | xk
( ) | ( ) | ( ) | ( | ) | ( | ) | ( | ) z | zk | y | yk | x | xk | Rz | zk | Ry | yk | Rx | xk
( ) | ( ) | ( ) | ( | ) | ( | ) | ( | ) z | zk | y | yk | x | xk | Rz | zk | Ry | yk | Rx | xk
( ) | ( ) | ( ) | ( | ) | ( | ) | ( | ) z | zk | y | yk | x | xk | Rz | zk | Ry | yk | Rx | xk
( ) | ( ) | ( ) | ( | ) | ( | ) | ( | ) z | zk | y | yk | x | xk | Rz | zk | Ry | yk | Rx | xk

(3-23)

Damit lässt sich die Differenziation der kinematischen Kette auf die Differenziation der Elementarmatrizen zurückführen. Da jeweils auch nur eine Elementartransformation vom Parameter

'
k p

abhängt, verschwinden die Ableitungen der Terme (3-23), die nicht von diesem Parameter abhängen.

Rotation; und
existieren:; Translation; für; sonst

13.05.2013 V3.4 | - 3-10 - | © Dr-Ing. habil. Jörg Wollnack

Die Ableitungen der homogenen⁴ Elementarmatrizen ergeben sich zu:

Translation

Analog lassen sich höhere Ableitungen beschreiben, wobei die Besonderheit auftritt, dass die Translationsterme verschwinden und lediglich höhere Ableitungen der Rotationsterme

(3-26)

4 Die Differenziation homogener Koordinaten führt zu der Gleichung:

'
' | ' | '
1
0 | 0
p | p | p
r | R | t | r

0

Hierbei ist darauf zu achten, dass die Matrizendifferenziation homogener Matrizen von der allgemeinen Definition der Matrixdifferenziale abweichen muss, weil man ansonsten nicht homogene Differenzialmatrizen erhält. Man kann dies erkennen, wenn man von
r R r t '

ausgeht. Aus

homogener Schreibweise die partiellen Ableitungen homogener Matrizen zu:

Dieser Umstand kann dadurch berücksichtigt werden, dass man in erst der resultierenden Produktmatrix T (3-19) den verschwindenden Maßstabsfaktor zu eins setzt. Dies gilt analog auch für die homogene Koordinate rH.

für R-Achsen; für T-Achsen; für R-Ac; hsen; für T-Ach; sen; mit; für; sonst; und

13.05.2013 V3.4 | - 3-11 - | © Dr-Ing. habil. Jörg Wollnack

Rotation

mit

(3-27)

Betrachtet man die Gleichung

1 | 1
' | '
0 | 1
n | k | G n
k
n | n j | j
p | p k | k j | j k

T
T | T | T , | (3-28)

so kann man die Produktterme durch ihre Transformationen

1 | 1
' | ' 0 | 1

n
k | G k
n | k
k | k p | p

T
T T | T

(3-29)

ersetzen. Mit (3-26) und (3-27) erhält man nach Multiplikation der Matrizen⁵:

R | e | . | (3-31)

Infolgedessen lässt sich das Differenzial der offenen kinematischen Kette analytisch beschreiben (siehe auch Anhang Kap. 3.7).

5 R steht für Rotation und T Translation.

mit; und; RTm

13.05.2013 V3.4 | - 3-12 - | © Dr-Ing. habil. Jörg Wollnack

## 3.3 Verallgemeinerte Taylorsche Reihe

Die
Tj

-Matrizen der kinematischen Transformation sind von den entsprechenden Transformationsparametern des Gelenkübergangs abhängig. Je nachdem, welche Beschreibungsform für diese Gelenkübergänge gewählt wird, hängt jede Matrix von einer bestimmten Anzahl von Parametern
p jk
'

ab:

T f

j | j p j | p j | p jk | p jb ( '
,

'

,...,

'

,...,

' )
1 | 2
. | (3-32)

Hierbei bezeichnet der erste Index die Nummer und der zweite Index den Parameter des Gelenkübergangs. Diese Parameter beschreiben sowohl stationäre Größen, z.B. Armlängen, als auch variable Größen, die Stellgrößen der Antriebe. Bei der Berechnung der Pose der kinematischen Transformationsmatrix

y pRPY (T)

(3-33)

werden

N G b
Parameter der Gelenkübergänge auf M 6

Transformationsparameter abgebildet:

' | : | ( ') N | M p | y | y f p . | (3-34)

Im Falle der hier diskutierten Roll-Pitch-Yaw-Transformation ist

b const 6
. Die Parameter
der Gelenkübergänge sind nur mit einer beschränkten Genauigkeit bekannt oder lassen sich hinsichtlich der Stellgrößen nur mit einer beschränkten Auflösung messen oder einstellen.

Die Fehlerfortpflanzungsanalyse erster Ordnung dieser Unsicherheiten der kinematischen Transformation wird im wesentlichen bereits durch die allgemeinen systemtheoretischen Darstellungen vollzogen, weshalb im Folgenden lediglich kurz die Möglichkeiten der analytischen Berechnung der partiellen Ableitungen der T-Matrizen [117] diskutiert wird.

Diese analytische Beschreibung ermöglicht eine geschlossene Berechnung der verallgemeinerten Taylorschen Reihe [31] der T-Matrix:

T(p') T(p' ) | T(p' ) | T(p' ) .... | T(p' ) R ( p') 0 | 0 | ! | !

Für den Differenzialoperator in (35.2) lässt sich die Identitätsaussage
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
k k | k | p

h

i | i

N

i

k

k | k | k | k | n

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
! | ! | ! | '

'
1 | 1 | 2 | 1 1 | 2 |

(3-36)

(Summe über alle N-Tupel verschiedener natürlicher Zahlen, für die gilt
ki N

)

angeben. Diese Beschreibung lässt sich in eine rekursive Form überführen:

T0 | R | p | T0 | 1 | T p

1
, | , | ! | 0
( | ') | ( ' ) m | Tm | m | m

m
d

, mit
T0,0 | T p 0
( ' ) . | (3-37)

13.05.2013 V3.4 | - 3-13 - | © Dr-Ing. habil. Jörg Wollnack

Die rekursive Beschreibung hat den Vorteil, dass bei einer Genauigkeitssteigerung nicht sämtliche Terme der verallgemeinerten Taylorschen Reihe neu zu berechnen sind. In der Praxis wird man sich meist auf lineare, quadratische und kubische Terme beschränken. Für weitere Einzelheiten und Anwendungsmöglichkeiten dieses Ansatzes sei auf [117, 166] verwiesen.

## 3.4 Inverse kinematische Transformation

Die Aufgabe der inversen kinematischen Transformation ist es, unter vorgegebener Pose die Gelenkkoordinaten zu berechnen. Die inverse kinematische Transformation ist nicht notwendigerweise eindeutig, so dass für eine Pose mehrere Lösungen existieren können. Diese Mehrdeutigkeiten können dazu genutzt werden, z. B. um Hindernisse herumzugreifen.

Die inverse kinematische Transformation

K | T | p | K T | T T t
I | v | I
: | ' | ( ) , | ( , | ) G
q
G

q
(3-38)

berechnet zu einer gegebenen Pose (t , ) G

q
G

q

t | t
t
des Endeffektorkoordinatensystems S

G
gegenüber dem Bezugskoordinatensystem S

q
die Werte der Gelenkvariablen
t | B
v | v | v( | 1) | v( | 1) ' | ( ' , ' | ,..., ' | ) | f
q | q | G p | p | p | p
(3-39)

der kinematischen Transformation.

Der Gelenkvariablenvektor
p'
v

enthält die nicht konstanten Elemente der Transformationsparametervektoren
p'
, | { , ,..., | } i
i | 0 1 | G 1

. Es existieren zumeist mehrere Lösungen, mit denen dieselbe Pose angefahren wird. Der durch den Vektor p'
v

aufgespannte Raum wird als Gelenkkoordinatenraum des IR und die Elemente des Gelenkkoordinatenvektors werden als Gelenkkoordinaten bezeichnet.

Die Problemstellung der inversen kinematischen Transformation erfordert die Lösung von G gekoppelten, nichtlinearen Gleichungen [24, 64, 76, 77, 133, 140, 173, 178]. Geschlossene analytische Lösungen sind nur für bestimmte Annahmen, wie z.B. der Parallelität oder der Orthogonalität der Gelenkachsen zueinander, entwickelt worden. Im Zusammenhang mit der Roboterparameteridentifikation der 3D-Modelle gilt es, gerade auch diese Parallelitäts- und Orthogonalitätsfehler zu identifizieren, so dass man in diesem Zusammenhang von den vereinfachenden Annahmen keinen oder nur in beschränkter Weise Gebrauch machen kann. Die Lösung der inversen kinematischen Transformation wird deshalb zumeist unter Anwendung numerischer Minimierungsverfahren vollzogen [24, 35, 133, 148]. Der Ansatz von Li [89] nutzt ein Bindungsgleichungssystem, um mit Hilfe einer Polynomgleichung und weiteren linearen Gleichungen sämtliche Lösungen der Gelenkkoordinaten zu berechnen. Dieser Ansatz führt letztlich auf die iterative Suche der Nullstellen der Polynomgleichung, weshalb man auch diese Methode in die Klasse der iterativen Verfahren einordnen muss. Für einen systematischen Vergleich verschiedener Verfahren der inversen Transformation sei auf Kreuzer [77] verwiesen.

13.05.2013 V3.4 | - 3-14 - | © Dr-Ing. habil. Jörg Wollnack

### 3.4.1 Singularitäten

Kinematische Robotermodelle besitzen sowohl kontante als auch zeitlich veränderliche Parameter. Singularitäten können sowohl aus der Sicht der konstanten als auch der Sicht der variablen Parameter auftreten. Unter einer Singularität wird ein Rangdefekt der Jacobi-Matrix im Sinne von

Rang | ( ' ) | Dim | ' v | v | v J p | p

(3-40)

verstanden. Man unterscheidet struktur- und lagebedingte Rangdefekte. Strukturbedingte Singularitäten sind konstruktiver Natur oder liegen in den Achsmodelle begründet. Lagebedingte Rangdefekte sind strukturspezifisch und treten bei bestimmten Gelenkstellungen auf. Damit zerfällt die Ranguntersuchung einer kinematischen Struktur in zwei Teile:

Die Parametersingularitäten

Rang | ( , ) | Dim p
J p x | p

(3-41)

und Antriebssingularitäten

Rang | ( , ) | Dim x
J p x | x . | (3-42)

Parametersingularitäten sind für die Parameteridentifikation und Antriebssingularitäten für das inverse kinematische Problem bedeutsam. Singularitäten können auf Flächen oder Punktmengen auftreten und kennzeichnen linear abhängige Parameter oder Eingangsgrößen. Von besonderem Interesse sind ausgezeichnete Punktsingularitäten der Antriebsgrößen innerhalb des Wertevorrats des TCP-Poseraums.

### 3.4.2 Klassische Ansätze

Die klassischen Lösungsverfahren können auf zwei Ansätze zurückgeführt werden:

Ansatz mit Taylorscher Reihe

Die Aufgabenstellung der Bestimmung der Stellwerte für eine mit dem Endeffektorkoordinatensystem anzufahrende Pose lässt sich auf die Taylorsche Reihendarstellung zurückführen, so dass man die linearisierte Parametervektoränderung über

1

v | v | v | RPY ' | ( ' ) | q
p | J p | pG

, mit

t
t | t
RPY | RPY

q
q
G | G
p | t

(3-43)

berechnen kann. Für den Fall einer quadratischen, nichtsingulären Jacobi-Matrix lässt sich die Aufgabenstellung lösen. Bei den nichtquadratischen Formen bedient man sich der Pseudoinversen der SVD-Zerlegung. Hieran zeigt sich die Bedeutung der Singularitäten für die Inversenberechnung. Dies wird auch noch einmal in Kap. 3.5 im Zusammenhang mit den Gelenkgeschwindigkeiten deutlich.

13.05.2013 V3.4 | - 3-15 - | © Dr-Ing. habil. Jörg Wollnack

Minimierungsproblem

Eine andere Interpretation der Aufgabenstellung führt zu einem Minimierungsproblem

t
t | t
' | RPY RPY,Soll
Min | ( ( ' ))
v p | v
t | p | T p | , | (3-44)

so dass für die Bestimmung des Gelenkvariablenvektors Verfahren Anwendung finden können, die sich der partiellen Ableitung der kinematischen Transformation bedienen.

Die o. g. Ansätze nutzen bei der iterativen Berechnung der Gelenkkoordinaten die partiellen Ableitungen der kinematischen Kette. Anstatt nummerische Differenziationsverfahren zu verwenden, ließe sich für eine Genauigkeitssteigerung und Beschleunigung der Berechnung der Gelenkkoordinaten die analytische Berechnung der partiellen Ableitungen heranziehen [117, 166]. Ferner kann der Startwert für eine weitere Beschleunigung der Verfahren über das vereinfachte parallelitäts- und orthogonalitätsfehlerfreie kinematische Modell des IR berechnet werden.

Minimierungsansätze haben zudem den Vorteil, dass sie bei Rangdefekten nicht versagen und mehrdeutige Lösungen produzieren, die für die Antriebe auch vorliegen. Deshalb kann man diese zur Inversenberechnung an ausgezeichneten Antriebssingularitäten einsetzen. Als Startwerte kann man Lösungen der Inversen in der Umgebung der ausgezeichneten Singularität heranziehen. Dies hat zudem zur Folge, dass man mit minimalen Veränderungen der Antriebsgrößen in die analytisch nicht berechenbare Endeffektorpose fährt.

Diese Möglichkeit der Inversenberechnung an ausgezeichneten Singularitäten ist insbesondere für den kooperierenden Betrieb eines Multi-Kinematik-Systems bedeutsam, weil man hiermit die Bewegungsrestriktionen des Gesamtsystems reduzieren kann. Die Iteration muss dabei unter Echtzeitbedingungen erfolgen, was keineswegs eine triviale Aufgabe darstellt.

trizen zu⁶:

13.05.2013 V3.4 | - 3-16 - | © Dr-Ing. habil. Jörg Wollnack

### 3.4.3 Analytische Inverse für ausgezeichnete Kinematiken

Eine analytische inverse kinematische Transformation mit sechs Freiheitsgraden lässt sich immer dann finden, wenn die serielle offenen kinematischen Kette so konstruiert ist, dass sowohl die Drehgelenksachsen orthogonal bzw. parallel ausgerichtet als auch die Position und Orientierung separierbar sind. Hierzu müssen sich die drei letzten Drehachsen des Handgelenks in einem Punkt, dem Wrist Center Point (WCP), schneiden (siehe Abb. 3-5).

Abb. 3-5: Fanuc Industrieroboter mit eingezeichneten Koordinatensystemen in Nulllage

Ausgehend von den Koordinatensystemen in Abb. 3-5 erhält man die Transformationsma-

6 Der kompakten Schreibweise wegen werden die Abkürzungen und Identitäten

cos( )cos( ) sin( )sin( ) cos( | ) Ci j | i | j | i | j | i | j

und

sin( )cos( ) cos( )sin( ) sin( | ) i j | i | j | i | j | i | j S

herangezogen.

Damit erhält man die Transformation

13.05.2013 V3.4 | - 3-17 - | © Dr-Ing. habil. Jörg Wollnack

Separationsansatz

Die TCP-Pose sei im Aktuatorkoordinatensystem über folgende Matrix

6
0
0 | 0 | 0 | 1
x | x | x | x
y | y | y | y
z | z | z | z
u | v | w | p
u | v | w | p
u | v | w | p
T | . | (3-46)

beschrieben. Für die gesamte kinematische Kette gilt:

6 | 1 | 2 | 3 | 4 | 5 | 6 T | T T T T T T 0 | 0 | 1 | 2 | 3 | 4 | 5
. | (3-47)

Diese kinematische Vorwärtstransformation wird so separiert, dass die erste Matrix

(3-48)

die Transformation vom WCP- ins Aktuatorkoordinatensystem und die zweite Matrix

(3-49)

die Transformation vom TCP- ins WCP-Koordinatensystem angibt. Weiter gilt dann:

6 | 3 | 6 T | T T 0 | 0 | 3
. | (3-50)

Position des Wrist Center Point

Die WCP-Position sei durch den Vektor

t

0

1

x | y | z q | q | q | q

(3-51)

beschrieben. Für die Position des WCP in Bezug auf den TCP gilt:

definiert. Mit der Transformation; multipliziert, lässt die Gleichung

13.05.2013 V3.4 | - 3-18 - | © Dr-Ing. habil. Jörg Wollnack

bzw.

6

6
0
6
1 | 1
x | x | x
y | y | y
z | z | z
q | p | d w
q | p | d w
q | p | d w
q | . | (3-54)

Hiermit lässt sich die WCP-Position in Bezug auf das Aktuatorkoordinatensystem für eine TCP-Pose angeben. Zudem ist die Position des WCP in Bezug auf das dritte Gelenk über

3

0
0
q

(3-55)

aufstellen. Diese Gleichung lässt sich mit der inversen von

(3-57)

umformen. Aus diesem Gleichungssystem lassen sich drei unabhängige Gleichungen für drei

Variablen bestimmen:

x | y 1 | 1 | 1 | 4 23 | 3 | 23 | 2 | 2 q C | q S | a | d S | a C | a C
(3-58)
z | 4 | 23 | 3 23 | 2 2 q | d C | a S | a S

(3-59)

1 | 1 | 0 x | y
q S | q C | . | (3-60)

Aus (3-60) lässt sich dann unmittelbar der Winkel

1

arctan 2( , )
y x

qq
(3-61)

berechnen. Die Variablen qx und qx sind über (3-54) bestimmt. Bildet man das Quadrat der ersten drei Zeilen (3-58) bis (3-60), so erhält man:

2 | 2 | 2
1 | 1 | 1 | 1
2 | 2 | 2 | 2
4 | 3 | 2 | 1 | 2 3 | 2 | 23 | 2 23 | 2 4 | 23 | 2 | 23 2
2 | 2
2 | ( | ) 2 | ( | )
x | y | z | x | y
q | q | q | a q C | a q S
d | a | a | a | a a C C | S S | a d S C | C S
. | (3-62)

13.05.2013 V3.4 | - 3-19 - | © Dr-Ing. habil. Jörg Wollnack

Mit den trigonometrischen Additionstheoremen

23 | 2 | 23 | 2 | 2 | 3 | 2 | 3 C C | S S | C cos( | ) | und | (3-63)
23 | 2 | 23 | 2 | 2 | 3 | 2 | 3 S C | C S | S sin( | )

(3-64)

kann man (3-62) zu

2 | 2 | 2 | 2 | 2 | 2 | 2
1 | 1 | 1 | 1 | 4 | 3 | 2 | 1 | 2 3 | 3 | 2 4 3 2 | 2 | 2 | 2
x | y | z | x | y
q | q | q | a q C | a q S | d | a | a | a | a a C | a d S

(3-65)

umformen. Da
| | 1

über (3-61) bestimmt ist, können die bekannten und konstanten Parameter zusammengefasst werden. Mit den Abkürzungen

1 | 2 4 2ad , | (3-66)
2 | 2 3 2aa
und | (3-67)
2 | 2 | 2 | 2 | 2 | 2 | 2
3 | 1 | 1 | 1 | 1 | 4 | 3 | 2 | 1 2 | 2 | ( | ) x | y | z | x | y q | q | q | a q C | a q S | d | a | a | a
(3-68)

erhält man für (3-65):

1 | 3 | 2 | 3 | 3 S | C | . | (3-69)

Und mit den trigonometrischen Beziehungen

2

2 tan
2
sin
1 tan
2

A

A
A

und

2

2

1 tan
2
cos
1 tan
2

A

A
A

(3-70.1-2)

können
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
(3-71)

durch

3
3 | 2
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
3 | 2
3

1
1

t
C
t

ersetzt werden, so

dass man die quadratische Gleichung

2
3 | 2 | 3 | 1 3 | 3 | 2 ( | ) | 2 | ( | ) 0 t | t

(3-72)

erhält. Deren zwei Lösungen

2 | 2 | 2
1 | 1 | 2 | 3
3;1,2
3 2

t
(3-73)

erlaubt über (3-71) eine Berechnung der Lösungen

3;1,2 | 3;1,2 2 arctan( | ) t | . | (3-74)

Dies sind die sogenannte rechts- und eine linksarmige Lösung den inversen Problems.

Damit ergibt sich nach (3-49) für
diesem Grunde wird die Rotationsmatrix; herangezogen.

13.05.2013 V3.4 | - 3-20 - | © Dr-Ing. habil. Jörg Wollnack

Aus (3-58) und (3-59) erhält man eine Beziehungen für
2

. Führt man hierzu die Abkürzungen

1 | 2 | 3 3 | 4 3 a | a C | d S , | (3-75)
2 | 3 3 | 4 | 3 a S | d C | , | (3-76)
1 | 3 3 | 4 | 3 a S | d C | und | (3-77)
2 | 2 | 3 3 | 4 3 a | a C | d S

(3-78)

ein, so erhält man ein lineares Gleichungssystem:

1 | 2 | 1 | 2 | 1 C | S

(3-79)

2 | 2 | 2 | 2 | 2 C | S | . | (3-80)

Mit der Cramerschen Regel erhält man die gesuchte Lösungen zu:

1 | 2 | 2 | 1
2
1 | 2 | 2 | 1
S | und | (3-81)
1 | 2 | 2 | 1
2
2 | 1 | 1 | 2
C | . | (3-82)

Damit lässt sich der Winkel
2

über

2 | 2 | 2 arctan 2( , | ) SC

(3-83)

berechnen. Für diesen Winkel existieren korrespondierend zu (3-74) ebenfalls zwei Lösungen.

Orientierung des Handgelenks

Nachdem sämtliche Winkel der ersten drei Antriebsachsen bestimmt sind, lassen sich die Winkel der letzten drei Antriebsachsen ermitteln. Aus der bereits bekannten kinematischen Kette

6 | 3 | 6 T | T T 0 | 0 | 3
folgt für die WCP-Transformation:

Für die verbleibenden Gelenkwinkel ist nur noch die Orientierung des TCP bedeutsam. Aus

(3-86)

gewinnt man die Gleichungen:; und
Hieraus lässt sich der Winkel

13.05.2013 V3.4 | - 3-21 - | © Dr-Ing. habil. Jörg Wollnack

Diese Transformationsmatrix ist bereits über (3-48) zu

1 | 23 | 1 | 1 23
3
0 | 1 | 23 | 1 | 1 23
23 | 23 0
C C | S | C S
S C | C | S S
S | | C

R

(3-87)

definiert. Da die Inverse dieser Matrix gleich ihrer Transponierten ist, erhält man:

1 | 23 | 1 | 23 | 23
3 | 1
0 | 1 | 1
1 23 | 1 23 | 23
( | ) | 0
C C | S C | S
S | C
C S | S S | C
R | . | (3-88)

Mit

6 | 3 | 1 | 6

über das Matrixelement 33 berechnen. Mit

(3-92)

ergibt sich

5;1,2 | 33 arccos( ) r | . | (3-93)

Für
5

existieren somit zwei Lösungen.

Aus den Matrixelementen 13 und 23 erhält man die Relationen

13
4
5

r
C
S
und | (3-94)

23
4
5

r
S
S

(3-95)

Damit gilt dann weiter:

23 13
4
5 | 5
arctan 2 | , r | r
SS
. | (3-96)

Link i; Gelenk i; Gelenk + 1 i

13.05.2013 V3.4 | - 3-22 - | © Dr-Ing. habil. Jörg Wollnack

Analog lässt sich auch
6

zu

32 | 31
6
5 | 5
arctan 2 | , r | r
S | S

(3-97)

berechnen. Für diese Winkel existieren korrespondierend zu (3-93) ebenfalls zwei Lösungen.

Damit sind sämtliche Gelenkwinkel bestimmt. Insgesamt existieren somit vier verschiedene Lösungen. Vor allem der dritten Achse kommt eine besondere Bedeutung zu, wenn es darum geht, Hindernisse zu umfahren.

Die nominellen Werte der DH-Transformation für das inverse Modell unterscheiden sich von denen der Vorwärtstransformation. Die entsprechenden Werte können der Tab. 3-5 entnommen werden (siehe auch Abb. 3-5 u. 3-6).

Abb. 3-6: DH-Parameter eines Gelenküberganges

i | θi | a / mm | d / mm | α / ° | 7θο / °
1 | θ1 | 312 | 0 | 90 | 0
2 | θ2 | 1075 | 0 | 0 | -90
3 | θ3 | 225 | 0 | 90 | 0
4 | θ4 | 0 | 1280 | -90 | 0
5 | θ5 | 0 | 0 | 90 | 0
6 | θ6 | 0 | 215 | 0 | 0

Tab. 3-5: DH-Parameter der Fanuc-Kinematik

Bemerkungen: Die Lage des Steuerungskoordinatensystems wird von vielen Roboterherstellern in die x/y-Ebene des Montageflansches in Abb. 3-5 gelegt. Dies ist im Hinblick auf die Kalibration der Robotermodelle nicht zweckmäßig, da hierdurch eine Linearkombination (Rangdefekt) des d-Parameters mit einem Translationsparameter zum externen Posemesssystem entsteht.

7 Diese Werte ergeben sich aus der vom Hersteller willkürlich definierten Nulllagenstellung der Maschine.

13.05.2013 V3.4 | - 3-23 - | © Dr-Ing. habil. Jörg Wollnack

## 3.5 Jacobi-Matrizen und kinematische Eigenschaften

Die Jacobi-Matrizen der Systemmodelle spielen eine zentrale Rolle in der Systemtheorie. Sie verknüpfen verschiedene Eigenschaften der Ein- und Ausgangssignale und charakterisieren das Fehlerfortpflanzungsverhalten erster Ordnung [201]. Zum Ende dieses Kapitels wird in Form einer Tabelle ein kompakter Überblick gegeben, um rückblickend die Bedeutung der Jacobi-Matrizen als Ganzes zu illustrieren.

### 3.5.1 Lokales Poseverhalten

Ausgehend von dem kinematischen Modell (3-8) und (3-33) mit einer Zerlegung nach Parametern p und Eingangsgrößen x

y f p x ( , )

(3-98)

erhält man über das totale Differenzial

( , ) d | ( , ) d i | i
i | i i | i
p | x
p | | x
f | f dy | p x | p x
(3-99)

bzw. mit den Jacobi-Matrizen kompakt

( , ) | ( , ) d y J p x dp J p x d x p | x
. | (3-100)

Im Allgemeinen verschwinden die Parameteränderungen, so dass man die in der Robotik gebräuchliche Form

( , ) dy J p x dx x

(3-101)

bzw.

1
( , ) dx J p x dy x

, mit

det | 0 x
J

(3-102)

erhält.

### 3.5.2 Geschwindigkeitsverhalten

Aus dem totalen Differenzial (3-99) erhält man die Relation

d | d ( , ) | ( , )
d | d | d
i | i
i | i i | i
| | p | | x
t | p | t | x | t
dy | f | f
v | p x | p x

(3-103)

bzw. mit den Jacobi-Matrizen kompakt

( , ) | ( , ) p | x y J p x p J p x x . | (3-104)

Infolgedessen hängen die Posegeschwindigkeiten über die Jacobi-Matrizen mit den Parameter- und Achsgeschwindigkeiten zusammen. Im Allgemeinen verschwinden die Parametergeschwindigkeiten, so dass man die in der Robotik gebräuchliche Form

( , ) x
y J p x x

(3-105)

13.05.2013 V3.4 | - 3-24 - | © Dr-Ing. habil. Jörg Wollnack

bzw.

1
( , ) x
x J p x y

, mit
det | 0 x
J

(3-106)

erhält.

### 3.5.3 Beschleunigungsverhalten

Das Beschleunigungsverhalten erhält man nach Differenziation von (3-103) unter Anwendung der Summen- und Produktregel zu:

2 | 2
2 | 2

2

| 2
d | d ( , ) | ( , )
d | d | d
d | d ( , ) | ( , )
d | d
i | i
i | i i | i
| | i | | i
i | i i | i
| | p | | p
t | t p | t | p | t
| | x | | x
t x | t | x | t
dy | f p x | f p x
f p x | f p x
. | (3-107)

Mit den Jacobi-Matrizen erhält man in kompakter Form die Gleichung

p | p | x | x y J p J p | J x J x , mit
( , ) , | ( , ) p | p | x | x J | J p x | J | J p x
(3-108)

bzw. in der Robotik bei verschwindenden Ableitungen der Parameter die gebräuchliche Form der Gleichung zu:

x x y J x J x

(3-109)

bzw. aus (3-106) zu:

1 | 1
x | x x J y J y

, mit

det | 0 x
J

und
det | 0 x
J | . | (3-110)

### 3.5.4 Ruck- und Pulsverhalten

In physikalischen Systemen, die durch Differenzialgleichungen n-ter Ordnung beschrieben werden, sollten Zustandsänderungen (n + 1)-fach stetig differenzierbar sein, damit keine Sprung- und Dirac-Funktionen⁸ auftreten, die physikalisch letztlich nicht realisierbar sind. Man nennt solche Zustandsänderungen ruck- und stoßfrei. Diese Bewegungen zeichnen sich zudem potenziell sowohl durch geringere Soll-Istfehler als auch einen materialschonenden, vibrationsarmen Betrieb aus.

In realen mechatronischen Systemen sind typischerweise Differenziale 3-ter Ordnung zu betrachten, da elektrische Spannungssprünge im Allgemeinen zulässig und näherungsweise realisierbar sind. Nach Anwendung der Produktregel erhält man aus (3-108) das Ruck- und Pulsverhalten zu:

8 Sprung- oder Pulsfunktionen bedingen Spektren der Art

1
(2 )
2

f
j f

oder
si( | ) sin( | ) / f | f | f

. Die

Dirac-Funktion hat als Spektrum eine konstante 1. Bei endlicher Bandbreite können diese Funktionen nicht existieren.

13.05.2013 V3.4 | - 3-25 - | © Dr-Ing. habil. Jörg Wollnack 2 | 2 x p | p | x | x p
y | J p | J p J p | J x | J x J x | (3-111)

Die in der Robotik bei verschwindenden Ableitungen der Parameter gebräuchliche Form ergibt sich dann zu:

2 x x | x y J x | J x J x

(3-112)

bzw. aus (3-110) zu:

1 | 1 | 1 2 x | x | x x J y | J y J y , mit
det | 0 x
J | , det | 0 x

J und
det | 0 x

J . (3-113)

### 3.5.5 Kraft- und Momentenverhalten

Unter der Annahme einer verlustlosen Bewegung einer masselosen kinematischen Struktur lässt sich aufgrund des Energieerhaltungssatzes eine Relation zwischen den verallgemeinerten Kräften im (G-1)-ten Koordinatensystem und den Antriebskräften herleiten.

Ausgehend von einer infinitesimalen Bewegung der Antriebs- und (G-1)-ten-Koordinaten dx
und
dy

erhält wegen der Äquivalenz der Energien

t | t Fyd | d Τx . | (3-114)

Hierbei repräsentiert F den verallgemeinerten Kraftvektor im (G-1)-ten Koordinatensystem und T den der Antriebskoordinaten. Da die infinitesimale Bewegung über die Jacobi-Matrix

d ( , ) d x
y J p x x

(3-115)

zusammenhängt, erhält man mit (3-114) weiter

t | t ( , ) d | d F J p x | x x | Τ | x , | (3-116)

so dass die Relation

t | t | ( , ) Τ | F J p x x
(3-117)

gilt. Mit

t
t | t A B | B A
lassen sich die verallgemeinerten Kräfte sodann über

t
( , ) Τ J p x F x

(3-118)

beschreiben. Damit stehen bei einer verlustlosen Kinematik die verallgemeinerten Antriebskräfte über die transponierten Jacobi-Matrix der Antriebskoordinaten mit den verallgemeinerten Kräften im (G-1)-ten Koordinatensystem in einem wohldefinierten Zusammenhang. Bei der Verwendung von elektrischen Antrieben kann man seinerseits die Antriebskräfte- bzw. -momente über die Motorströme und Motorkonstanten bestimmen, so dass eine Messung der verallgemeinerten Kräfte im (G-1)-ten Koordinatensystem möglich wird. Treten nicht zu große Verluste auf, so lassen sich diese Gleichungen zur Abschätzung der Kräfte heranziehen.

Die Jacobi-Matrizen können analytisch über die Ansätze im Kap. 3.2 bestimmt werden, so dass eine Berechnung selbst unter zeitkritischen Bedingungen möglich ist.

, verlust- und massefreie Kinematik; Kinematisch invers; , mit det; und; det; , det; Kinematisch invers rekursive Alternative

13.05.2013 V3.4 | - 3-26 - | © Dr-Ing. habil. Jörg Wollnack

### 3.5.6 Übersicht

Stationäres explizites parametrisches Steuerungsmodell:

, | ( , ) P M | N p x | y | y f p x D | W f | y
, mit | ( , ) | ( , ) x | x

f
J | J p x | p x
x

(3-119)

Positions-, Geschwindigkeits-, Beschleunigungs-, Stoss- und Ruck- sowie Kraftverhalten:
Kinematisch vorwärts
(3-120)
(3-121)
(3-122)
(3-123)
, mit det | 0 x
J

(3-131)

, mit det | 0 x
J

(3-132)

, mit det | 0 x
J

(3-133)

Technische Restriktionen:
Max x t | v () | und
Max x t | a ()
, mit
{1,..., }f

(3-134)

Unsicherheiten:
Implizites Modell
I p y x | f p y x | 0 | y f p x , , | ( , , ) | ( , ) DW f | y

(3-135)
Systematische Fehler

1
Max m | mn | mn | m | mn | m
yxp | y | x | p J | J | x | J | p

(3-136)

Zufällige Fehler

t
S | Q S Q y | yx | x | yx ' | ' | '

, mit

1
' | ' ( , , ) | ( , , ) Q | J | p x y J p x y yx | y | x
, | (3-137)
' | ' | ' ' | '
m | x | n | x m | n
E x | x SX
, | (3-137)
i | j
SY | E y | y i | y | j | y
und | (3-137)

t
t | t x | x p '
(3-138)

Tab. 3-6: Jacobi-Matrizen und kinematisches Systemverhalten

η-ter Slave- Aktuator; m-ter Master- Aktuator; Objekt; TCP; TCP η; TCP m

13.05.2013 V3.4 | - 3-27 - | © Dr-Ing. habil. Jörg Wollnack
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

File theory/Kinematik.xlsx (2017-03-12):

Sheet: Kinematik
Forward kinematics
 |  |  |  |  | WCP | 199.7
 |  |  |  |  |  | 10.5
 |  |  |  |  |  | 400.0
 |  |  |  |  | TCP | 339.53 | -90.0 | 30.0
 |  |  |  |  |  | 17.79 | -60.0 | 1e-05
 |  |  |  |  |  | 400.00 | -87.0 | 3.0
 |  |  |  |  |  |  |  |  |  |  |  |  |  |  |  |  | Achtung: in Excel ARCTAN2(x;y) entspricht ARCTAN(y/x) (falschrum!)
Joint Angles |  |  | Inverse Kinematics
 |  |  | looking forward |  |  |  | looking backward
q0 | 3.0 ° | 0.05 RAD |  | 3.0 ° |  |  |  | -177.0 ° | switch direction when necessary to make it stetig
q1 | 0.0 ° | 0.00 RAD | 0.00 ° | 67.38 ° |  |  | -67.38 ° | 0.00 ° |  |  |  |  |  |  |  |  |  |  |  |  | Ursprung
q2 | 0.0 ° | 0.00 RAD | 0.00 ° | -180.00 ° |  |  | 0.00 ° | -180.00 ° |  |  |  |  |  |  |  |  |  |  |  |  | 0
q3 | 0.0 ° | 0.00 RAD |  |  | 1.138951898e-08 ° | -180.00 ° |  |  |  |  |  |  |  |  |  |  |  |  |  |  | 0
q4 | 1e-05 ° | 1.745329252e-07 RAD |  |  | 9.993164315e-06 ° | -9.993164315e-06 ° |  |  |  |  |  |  |  |  |  |  |  |  |  |  | 0
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

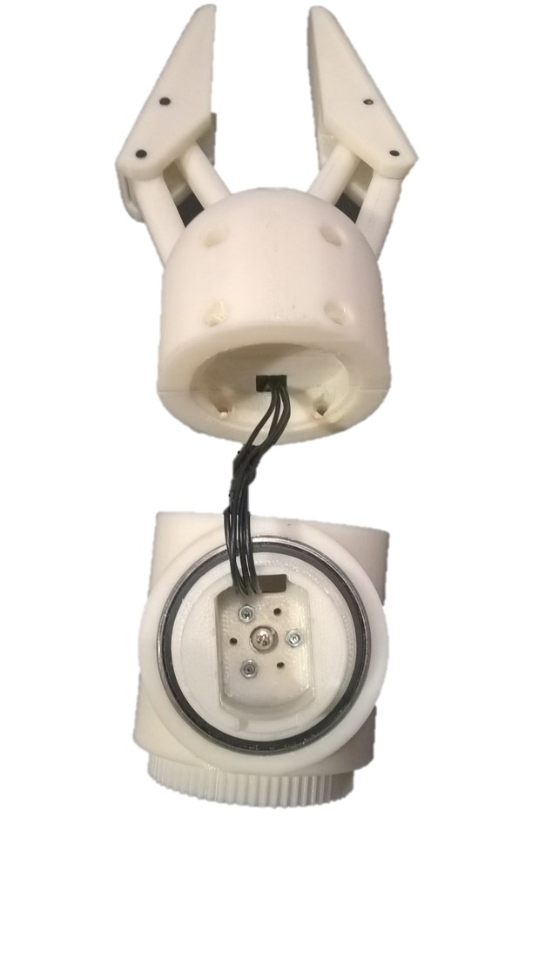
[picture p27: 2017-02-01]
docs/galery/gripperwrist3.jpg

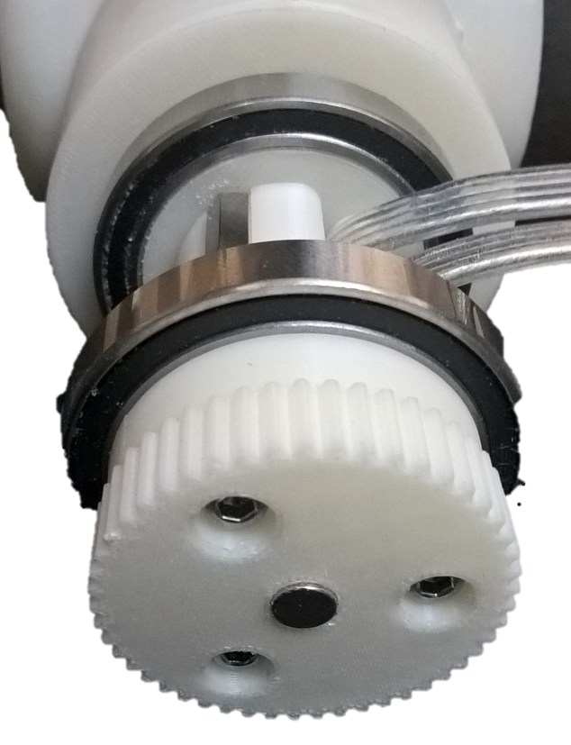
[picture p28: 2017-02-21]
docs/galery/elbow1.png

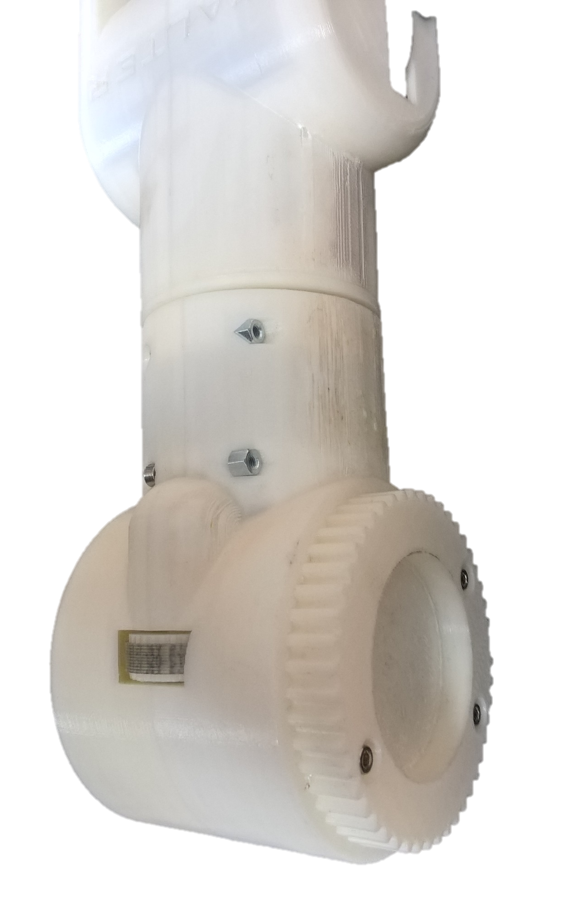
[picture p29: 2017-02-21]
docs/galery/elbow2.png

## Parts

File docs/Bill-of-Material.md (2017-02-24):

This is the list of main components. Besides that, a lot of incidentals (screws etc.) have been necessary

|Category |  #| What | From |
|:---|--:|:---|:---|
|3D Print | 1 | 3D printer (ABS) | Zortrax M200 |
| | | Petroleum, Acetone | Local Dealer |
|Electronics | 5 | Stepper Driver, TB 6600, 4A current | Pibot Stepper Driver 2.2, www.pibot.com | 
| | 1 | Walters Cortex: ARM M4 | Teensy 3.5, www.pjrc.com |
| | 1 | Walters Cerebellum: ARM A15, 2.0Ghz , running Linux| Odroid XU4, www.hardkernel.com |
| | 5 | Magnetic Encoder | AMS AS5048B, www.digikey.com |
| | 1 | Power supply for steppers 24V, 10A | S-250-24, www.omc-stepperonline.com |
| | 1 | Power supply for electronics and servos 12V1A/5V5A | Meanwell RD35A |
|Motors | 2 | Robot Servos for gripper and hand | HerkuleX Servo DRS-101, www.robotshop.com |
| | 1 | Stepper motor wrist, Nema 17, 42x42x39, 0.40Nm | 17HS-0404S, www.omc-stepperonline.com|
| | 1 | Stepper motor elbow, Nema 17, 42x42x25, 0.17Nm | 17HS10-0704S, www.omc-stepperonline.com  |
| | 1 | Stepper motor forearm, Nema 24, 60x60x57, 1.9Nm | Nanotec ST6018M2008|
| | 1 | Stepper motor upperarm, Nema 24, 60x60x88, 3.1Nm | Global Biz, GB24H288-40-4A|
| | 1 | Stepper motor hip, Nema 23, 57x57x56, 1.3Nm | 23HM22-2804S, www.omc-stepperonline.com  |
|Belt Drive Forearm | 1 | Timing Pulley T2.5, 6mm, 15 Teeth | www.cncshop.at |
| | 1 | Toothed Belt T2.5 6mm, 250mm length | www.cncshop.at|
|Belt Drive Elbow | 1 | Timing Pulley T2.5, 6mm, 14 Teeth | www.cncshop.at|
| | 1 | Toothed Belt T2.5 6mm, 145mm length | www.cncshop.at|
| | 1 | Toothed Belt T2.5 6mm, 120mm length |  www.cncshop.at|
|Belt Drive Upperarm| 1 | Timing Pulley T5, 10mm, 14 Teeth |  www.cncshop.at|
| | 1 | Timing Pulley T5, 10mm, 15 Teeth |  www.cncshop.at|
| | 1 | Timing Pulley T5, 10mm, 48 Teeth |  www.cncshop.at|
| | 1 | Toothed Belt T5 10mm, 375mm length |  www.cncshop.at|
| | 1 | Toothed Belt T5 10mm, 430mm length |  www.cncshop.at|
|Belt Drive Shoulder| 1 | Timing Pulley T5, 10mm, 14 Teeth |  www.cncshop.at|
| | 1 | Timing Pulley T5, 10mm, 14 Teeth |  www.cncshop.at|
| | 1 | Timing Pulley T5, 10mm, 48 Teeth |  www.cncshop.at|
| | 1 | Toothed Belt T5 10mm, 340mm length |  www.cncshop.at|
| | 1 | Toothed Belt T5 10mm, 450mm length |  www.cncshop.at|
|Belt Drive Hip | 1 | Timing Pulley T5 10mm, 10 Teeth |  www.cncshop.at|
| | 1 | Toothed Belt T5 10mm, 510mm length |  www.cncshop.at|
|Gripper Bearings |16 | 3x7x3m | www.kugellager-express.de |
|Wrist Bearings | 1 | DIN 625 SKF - 61807 35x47x7mm | www.kugellager-express.de |
| | 1 | DIN 625 SKF - 61807 35x44x5mm | www.kugellager-express.de |
| | 1 | DIN 625 SKF - 61902 15x28x7mm | www.kugellager-express.de |
|Forearm Bearings | 2 | 3x10x4mm | www.kugellager-express.de |
|Elbow Bearings | 2 | DIN 625 SKF - 61807 35x47x7mm | www.kugellager-express.de |
| | 2 | 6x19x6 | www.kugellager-express.de |
| | 4 | 3x10x4 | www.kugellager-express.de |
|Upperarm Bearings  | 2 | DIN 625 SKF - 61807 35x47x7mm | www.kugellager-express.de |
| |16 | 4x13x5 | www.kugellager-express.de |
| | 2 | 8x22x7 | www.kugellager-express.de |
|Shoulder Bearings  | 6 | 4x13x5 | www.kugellager-express.de |
| | 2 | 8x22x7 | www.kugellager-express.de |
| | 2 | DIN 625 SKF - SKF 61818 - 80x100x10 | www.kugellager-express.de |
|Hip Bearings | 1 | DIN 625 SKF - SKF 61818 - 90x115x13 | www.kugellager-express.de |
| | 6 | 4x13x5 | www.kugellager-express.de |
|Housing Bearings |16 | 3x8x3 | www.kugellager-express.de | 

Note: all bearings are deep groove ball bearing, dimensions are given in diameter inside/diameter outside/width in mm.

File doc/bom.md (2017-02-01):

	
# Bill of Material 

Main components:
	
| | What | From |
|--- |---|---|
| 1 | 3D printer (ABS) | Zortrax M200
| 5 | Stepper Driver, TB 6600, 4A current | Pibot Stepper Driver 2.4 | 
| 2 | Robot Servos for gripper and hand | HerkuleX Servo DRS-101 |
| 1| Power supply for steppers 24V, 10A| www.omc-stepperonline.com S-250-24|
| 1| Power supply for electronics and servos 12V 1A / 5V5A| Meanwell RD35A|
| 1| Walters Cortex: ARM M4| Teensy 3.5|
| 1| Walters Cerebellum: ARM A15, 2.0Ghz , running Linux| Hardkernel, Odroid XU4|
| 1| Stepper motor wrist, Nema 17, 42x42x39, 0.40Nm| www.omc-stepperonline.com  17HS-0404S|
| 1| Stepper motor elbow, Nema 17, 42x42x25, 0.17Nm| www.omc-stepperonline.com  17HS10-0704S|
| 1| Stepper motor forearm, Nema 24, 60x60x57, 1.9Nm| Nanotec ST6018M2008. This one is expensive. Any other no longer than 68mm with similar torque works as well.|
| 1| Stepper motor upperarm, Nema 24, 60x60x88, 3.1Nm| Global Biz, GB24H288-40-4A|
| 1| Stepper motor hip, Nema 23, 57x57x56, 1.3Nm| www.omc-stepperonline.com  23HM22-2804S|

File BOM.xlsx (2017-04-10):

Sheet: Kräfte
 |  | Walter
Oberarm |  | 400 | [mm]
Unterarm |  | 270 | [mm]
Hand |  | 100 | [mm]
Sollgewicht |  | 0.80 | [kg]
Oberarmgewicht |  | 0.97 | [kg]
Unterarmgewicht |  | 0.87 | [kg]
Handgewicht |  | 0.39 | [kg]
Übersetzung Hüfte |  | 9.0 | [1:]
 | Zahnriemen Teilung | 5 | [mm]
 | Zahnriemenscheibe 1 Zähne | 10 | [Zähne]
 | Zahnriemenscheibe 1 Durchmesser | 15.9 | [mm]
 | Zahnriemenscheibe 2 Zähne | 90 | [Zähne]
 | Zahnriemenscheibe 2 Durchmesser | 143.2 | [mm]
Übersetzung Schulter |  | 17.63265306 | [1:] |  | Schulter ist etwas langsam vielleicht 1:17
 | Zahnriemen Teilung | 5 | [mm]
 | Zahnriemenscheibe 1 Zähne | 14 | [Zähne] |  | Hier ist Platz für bis zu 18Z
 | Zahnriemenscheibe 1 Durchmesser | 22.3 | [mm]
 | Zahnriemenscheibe 2 Zähne | 48 | [Zähne]
 | Zahnriemenscheibe 2 Durchmesser | 76.4 | [mm]
 | Zahnriemenscheibe 3 Zähne | 14 | [Zähne] |  | Platz für 15
 | Zahnriemenscheibe 3 Durchmesser | 22.3 | [mm]
 | Zahnriemenscheibe 4 Zähne | 72 | [Zähne]
 | Zahnriemenscheibe 4 Durchmesser | 114.6 | [mm]
Übersetzung Oberarm |  | 13.7 | [1:] |  | Oberarm ist eigentlich mit 8 mikroschritten ok,chneller wären gut, 1:9, dann könnte man auf 16 mikroschritte gehen, also aus dem 14Z ein 15Z machen
 | Zahnriemen Teilung | 5 | [mm]
 | Zahnriemenscheibe 1 Zähne | 14 | [Zähne] |  | An der Zwischenwelle ist Platz für bis zu 15Z
 | Zahnriemenscheibe 1 Durchmesser | 22.3 | [mm]
 | Zahnriemenscheibe 2 Zähne | 48 | [Zähne]
 | Zahnriemenscheibe 2 Radius | 76.4 | [mm]
 | Zahnriemenscheibe 3 Zähne | 15 | [Zähne] |  | riemen reicht nur fü 15Z, größer geht nicht
 | Zahnriemenscheibe 3 Durchmesser | 23.9 | [mm]
 | Zahnriemenscheibe 4 Zähne | 60 | [Zähne]
 | Zahnriemenscheibe 4 Durchmesser | 95.5 | [mm]
Übersetzung Handgelenkdreher | Ellbogen | 7.4 | [1:] |  | ok
 | Zahnriemen Teilung | 2.5 | [mm]
 | Zahnriemenscheibe 1 Zähne | 14 | [Zähne]
 | Zahnriemenscheibe 1 Durchmesser | 11.1 | [mm]
 | Zahnriemenscheibe 2 Zähne | 34 | [Zähne]
 | Zahnriemenscheibe 2 Durchmesser | 27.1 | [mm]
 | Zahnriemenscheibe 3 Zähne | 16 | [Zähne]
 | Zahnriemenscheibe 3 Durchmesser | 12.7 | [mm]
 | Zahnriemenscheibe 4 Zähne | 49 | [Zähne]
 | Zahnriemenscheibe 4 Durchmesser | 39.0 | [mm]
Übersetzung HandgelenkNicker |  | 4.3 | [1:]
 | Zahnriemen Teilung | 2.5 | [mm]
 | Zahnriemenscheibe 3 Zähne | 15 | [Zähne] |  | Platz ist bis 18Z
 | Zahnriemenscheibe 3 Durchmesser | 11.9 | [mm]
 | Zahnriemenscheibe 4 Zähne | 65 | [Zähne]
 | Zahnriemenscheibe 4 Durchmesser | 51.7 | [mm]
Drehmoment Zuschlag |  | 30%
Erdbeschleuinigung |  | 9.81 |  | [m/s^2]
Sollbeschleunigung |  | 4.905 |  | [m/s^2]
Roboterschwerpunkt |  | 385.00 |  | [mm]
Drehmoment Schulter |  | 8.4 |  | [Nm]
Drehmoment Oberarm |  | 34.3 |  | [Nm]
Drehmoment Unterarm |  | 11.22 |  | [Nm]
Drehmoment Handgelenkdreher |  | 0.58 |  | [Nm]
Drehmoment Handgelenk |  | 0.58 |  | [Nm]
Drehmoment Schulter Motor |  | 0.94 |  | [Nm]
Drehmoment Oberarm Motor |  | 1.95 |  | [Nm]
Drehmoment Unterarm Motor |  | 0.82 |  | [Nm]
Drehmoment HandgelenkDreher Motor |  | 0.08 |  | [Nm]
Drehmoment HandgelenkNicker Motor |  | 0.13 |  | [Nm]

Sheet: Zahnriemenscheiben
Teilung 2,5
Bezugsquellen
http://www.modellbauershop.de/antrieb/zahnriemenscheiben-teilung-t-25.php
http://www.modellbauershop.de/antrieb/zahnriemen-fuer-teilung-25.php
http://www.cncshop.at/index.php?k=798
http://www.hug-technik.com/shop/product_info.php
Berechnung
http://smarthost.maedler.de/maedlertools/maedler.html
Berechnung Zahnriemenscheibe T2,5
Zähne | 65 |  | Biegeradius Riemen | 0.55
Wirkdurchmesser | 51.73 | [mm] | Winkel | 0.3880001183 | 22.2
Außendurchmesser | 51.18 | [mm] | Trapezlänge oben | 1.010313595 | 1.053368245 | 0.009866140633
Innendurchmesser | 49.18 | [mm] | Schnitt außen | 52.90568822
Schnitt außen | 52.91 |  | Riemenbiegestelle trapezlänge | 1.021171799
 |  |  | zahnoberkantelänge | 1.22925767
Berechnung Zahnriemenscheibe T5
Zähne | 90
Wirkdurchmesser | 143.24 | [mm]
Außendurchmesser | 142.39 | [mm]
Tascheinnendurchmesser | 140.59 | [mm]
Winkeleckeinnendurchmesser | 138.59 | [mm]

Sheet: DIN
Kugelkopf M3 2 mm Duraluminium

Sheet: Rotary Encoder
Eval Board | AS5048
Bezugsquelle
http://www.mouser.de/ProductDetail/ams/AS5048B-TS_EK_AB/?qs=sGAEpiMZZMvc81WFyF5EdoQL2wnmmwE79zX4h9RmJyQ%3d
http://www.digikey.de/product-detail/de/ams/AS5048B-TS_EK_AB/AS5048B-AB-1.0-ND/3188613
Operational Manual
http://www.mouser.com/ds/2/588/AS5048-EK-AB_Operation-Manual_Rev.1.3-820438.pdf
Arduino lib
https://github.com/sosandroid/AMS_AS5048B
Sensor |  |  | PCB Board
5V | rot |  | 5V
SDA | grün |  | SCL
SCL | weiß |  | SDA
GND | schwarz |  | GDN
 | I2C address | A1 | A2
wrist | 0x44(reprogged from 0x40)
ellbow | loo0 | VDD
upperarm | 0x42 |  | VDD
shoulder | 0x43 | 1 | 1
hips | 0x44

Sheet: Herkulex Servo
HerkuleX Servo DRS-0101
Tutorial | http://robottini.altervista.org/dongbu-herkulex-arduino-library-2
Arduino library | http://robottini.altervista.org/wp-content/uploads/2012/12/Herkulex.zip
 |  | Kabel
 |  | blau | GND
 |  | rot | VDD
 |  | grün | TXD
 |  | schwarz | RXD

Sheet: Teensy 3.5
Teensy 3.5

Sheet: PiBot Stepper Driver
PiBot Stepper Driver
http://www.pibot.com/pibot-stepper-driver-rev2-2.html
 | en
Micro-stepping Setting

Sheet: BOM
 | Number | Article | Used in Component | Dealer |  |  |  |  |  |  | Status | -
Greifer
 | 16 | Rillenkugellager 3x7x3 | Lager für Greifer |  |  |  |  |  |  |  | Habs
 | 126 | Silberstahlwelle 3mm Durchmesser | Achsen für Greifer und Zahnräder, 4x 20mm, 2x23 mm |  |  |  |  |  |  |  | Habs
 | 6 | Zylinderkopfschraube Innensechskant M3 20mm | Verschraubung von Greiferkorpus |  |  |  |  |  |  |  | Habs
 | 1 | Distanzbolzen 2x Innen M3 20mm, Schlüsselweite 5,5mm | Verschraubung von Flansch mit Greiferkorpus |  |  |  |  |  |  |  | -
 | 2 | Distanzbolzen 2x Innen M3 20mm, Schlüsselweite 5,5mm | Verschraubung von Flansch mit Greiferkorpus |  |  |  |  |  |  |  | -
 | 4 | Zylinderkopfschraube Innensechskant M3 20mm | Verschraubung von Flansch mit Greiferkorpus |  |  |  |  |  |  |  | Habs
 | 2 | Zylinderkopfschraube Innensechskant M3 20mm | Greiferstreben Lagerachse am Greiferkorpus |  |  |  |  |  |  |  | Habs
 | 2 | Muttern M3, Schlüsselweite 5.5 mm | Greiferstreben Lagerachse am Greiferkorpus
 | 1 | Herkulex Servo DRS - 0101 | Antrieb Greifer |  |  |  |  |  |  |  | -
Handgelenk
 | 1 | Rillenkugellager DIN 625 SKF - 61807 35x47x7mm | Lager zum Greiferflansch |  |  |  |  |  |  |  | 0
 | 4 | Zylinderkopfschraube Innensechskant M2 6mm | Befestigung Lagerdeckel |  |  |  |  |  |  |  | Habs
 | 4 | Zylinderkopfschraube Innensechskant M2 12mm | Befestigung Servo |  |  |  |  |  |  |  | 0
 | 1 | Rillenkugellager DIN 625 SKF - 61902 15x28x7mm | Lagerung Handgelenk |  |  |  |  |  |  |  | 0
 | 1 | Rillenkugellager DIN 625 SKF - 61807 35x44x5mm | Lagerung Handgelenk Servoseite |  |  |  |  |  |  |  | Habs
 | 1 | Herkulex Servo DRS - 0101 | Antrieb Handgelenk |  |  |  |  |  |  |  | -
Unterarm
 | 1 | Zahnriemenscheibe T2,5, 15 Zähne (d=11,94) | Zahnriemenscheibe |  |  |  |  |  |  |  | Habs
 | 1 | Zahnriemen T2,5 250mm 6mm Breite | Zahnriemen zwischen Motor und Zahnriemenscheibe des Handgelenks |  |  |  |  |  |  |  | Habs
 | 1 | NEMA 17 - 42x42x34 - 0,26Nm - 5mm Achse - 0.4A 12V - 17HS13-404s | Antrieb Unterarm |  |  |  |  |  |  |  | Habs
 | 2 | Zylinderkopfschraube Innensechskant M3 20mm | Befestigung Motor |  |  |  |  |  |  |  | Habs
 | 1 | Zylinderkopfschraube Innensechskant M3 20mm | RiemenSpanner Schraube |  |  |  |  |  |  |  | Habs
 | 2 | Rillenkugellager 3x10x4 | Riemenspanner Kugellager |  |  |  |  |  |  |  | Habs
 | 1 | Vierkant Mutter M3 Breite 5.5mm | Riemenspanner Gegenverschraubung |  |  |  |  |  |  |  | Habs
 | 4 | Zylinderkopfschraube Innensechskant M2 6mm | Sensor Befestigung |  |  |  |  |  |  |  | Habs
 | 1 | Rotary Sensor | Winkelmesser Unterarm |  |  |  |  |  |  |  | Habs
 | 3 | Distanzbolzen 2x Innen M3 20mm, Schlüsselweite 5,5mm | Unterarm Verschraubung |  |  |  |  |  |  |  | -
 | 4 | Zylinderkopfschraube Innensechskant M3 30mm | Unterarm Verschraubung |  |  |  |  |  |  |  | Habs
 | 2 | Zylinderkopfschraube Innensechskant M3 20mm | Unterarm Verschraubung |  |  |  |  |  |  |  | Habs
 | 3 | Distanzbolzen 2x Innen M3 20mm, Schlüsselweite 5,5mm | Ellbogenflansch verschraubung |  |  |  |  |  |  |  | -
 | 6 | Zylinderkopfschraube Innensechskant M3 20mm | Ellbogenflansch verschraubung |  |  |  |  |  |  |  | Habs
Ellbogen | 2 | Rillenkugellager DIN 625 SKF - 61807 35x47x7mm | Lagerung Wrist |  |  |  |  |  |  |  | 0
 | 2 | RillenKugellager 6x19x6 | Lagerung Zwischenwelle |  |  |  |  |  |  |  | Habs
 | 4 | Rillenkugellager 3x10x4 | Lagerung RiemenSpanner |  |  |  |  |  |  |  | Habs
 | 40 | Silberstahlwelle 6mm Durchmesser | Welle Zwischenwelle |  |  |  |  |  |  |  | Habs
 | 42 | Silberstahlwelle 3mm Durchmesser | Welle Riemenspanner |  |  |  |  |  |  |  | Habs
 | 1 | Metallbohrer 6mm | Achse Zwischenwelle |  |  |  |  |  |  |  | 0
 | 1 | Gewindeschneider M3 | Achse Zwischenwelle |  |  |  |  |  |  |  | Habs
 | 1 | Metallbohrer 2.5mm (als M3 Kernlochborer) | Achse Zwischenwelle |  |  |  |  |  |  |  | Habs
 | 3 | Zylinderkopfschraube Innensechskant M3 20mm | Gehäuse Verschraubung am Handgelenk |  |  |  |  |  |  |  | Habs
 | 6 | Zylinderkopfschraube Innensechskant M3 25mm | Gehäuse Verschraubung im Kern |  |  |  |  |  |  |  | 0
 | 4 | Distanzbolzen 2x Innen M3 20mm, Schlüsselweite 5,5mm | Gehäuse Verschraubung im Kern |  |  |  |  |  |  |  | -
 | 1 | NEMA 17 - 42x42x21 - 0,73Nm - 5mm Achse - 1.2A | Motor |  |  |  |  |  |  |  | 0
 | 1 | Rotary Sensor | Sensor |  |  |  |  |  |  |  | Habs
 | 1 | Zahnriemen T2,5 145mm 6mm Breite | Zahnriemen Motor/ZwischenWelle (Länge ohne Spanner 175 |  |  |  |  |  |  |  | Habs
 | 1 | Zahnriemen T2,5 120mm 6mm Breite | Zahnriemen ZwischenWelle/WristFlansch (Länge 121 bei Z22 Zähne Rad) |  |  |  |  |  |  |  | Habs
 | 1 | Zahnriemenscheibe T2,5, 14 Zähne (d=9,55) | Zwischenwelle Zahnriemenscheibe Motor/Zwischenwelle |  |  |  |  |  |  |  | Habs
Oberarm | 4 | Zylinderkopfschraube Innensechskant M2 6mm | Sensor Befestigung |  |  |  |  |  |  |  | Habs
 | 1 | Rotary Sensor | Sensor |  |  |  |  |  |  |  | Habs
 | 2 | Unterlegscheiben M2 Dicke 0,5mm | Sensor befestigung |  |  |  |  |  |  |  | Habs
 | 2 | Rillenkugellager DIN 625 SKF - 61807 35x47x7mm | Lagerung Ellenbogen |  |  |  |  |  |  |  | 0
 | 4 | Senkkopfschraube Innensechskant M3 10mm | Befestigung Sensordeckel |  |  |  |  |  |  |  | Habs
 | 4 | Senkkopfschraube Innensechskant M3 10mm | Befestigung Kabelkanaldeckel |  |  |  |  |  |  |  | Habs
 | 4 | Zylinderkopfschraube Innensechskant M3 40mm | Befestigung Gabel/Block lange Befestigung |  |  |  |  |  |  |  | Habs
 | 4 | Zylinderkopfschraube Innensechskant M3 30mm | Befestigung Gabel/Block kurze Befestigung |  |  |  |  |  |  |  | Habs
 | 8 | Muttern M3, Schlüsselweite 5.5 mm | Befestigung Gabel/Block kurze Befestigung |  |  |  |  |  |  |  | -
 | 4 | Zylinderkopfschraube Innensechskant M3 45mm | Riemenspanner Gabel/Block |  |  |  |  |  |  |  | Habs
 | 8 | Rillenkugellager 4 x13 x 5 mm mit Flansch | Riemenspanner Gabel/Block |  |  |  |  |  |  |  | Habs
 | 4 | Rillenkugellager 4 x13 x 5 mm | Riemenspanner Gabel/Block |  |  |  |  |  |  |  | Habs
 | 40 | Rohr 4mmx3.1mm (=M3) | Riemenspanner Gabel/Block |  |  |  |  |  |  |  | -
 | 1 | Madenschraube M3 16mm | Riemenspanner Gabel/Block |  |  |  |  |  |  |  | Habs
 | 72 | Silberstahlwelle 8mm Durchmesser | Riemenscheibenachse |  |  |  |  |  |  |  | 0
 | 2 | Madenschraube M3 5mm | Riemenscheibenachse |  |  |  |  |  |  |  | Habs
 | 2 | Rillenkugellager 8x22x7 | Riemenscheibenachse |  |  |  |  |  |  |  | Habs
 | 4 | Zylinderkopfschraube Innensechskant M3 45mm | Befestigung Block/Basis |  |  |  |  |  |  |  | Habs
 | 4 | Vierkant Mutter M3 Breite 5.5mm | Befestigung Block/Basis |  |  |  |  |  |  |  | Habs
 | 1 | Zylinderkopfschraube Innensechskant M3 45mm | Riemenspanner Motor |  |  |  |  |  |  |  | Habs
 | 1 | Vierkant Mutter M3 Breite 5.5mm | Riemenspanner Motor |  |  |  |  |  |  |  | Habs
 | 2 | Rillenkugellager 4 x13 x 5 mm | Riemenspanner Motor |  |  |  |  |  |  |  | Habs
 | 40 | Rohr 4mmx3.1mm (=M3) | Riemenspanner Motor |  |  |  |  |  |  |  | -
 | 4 | Senkkopfschraube Innensechskant M3 10mm | Befestigung Lagerdeckel |  |  |  |  |  |  |  | Habs
 | 8 | Zylinderkopfschraube Innensechskant M3 20mm | Verbindung Befestigung Basishälften |  |  |  |  |  |  |  | Habs
 | 4 | Distanzbolzen 2x Innen M3 20mm, Schlüsselweite 5,5mm | Verbindung Befestigung Basishälften |  |  |  |  |  |  |  | -
 | 4 | Zylinderkopfschraube Innensechskant M3 30mm | Befestigung Motordeckel |  |  |  |  |  |  |  | Habs
 | 1 | Zahnriemen T5 375mm 10mm Breite | Zahnriemen Motor/Zwischenwelle |  |  |  |  |  |  |  | 0
 | 1 | Zahnriemen T5 430mm 10mm Breite | Zahnriemen Zwischenwelle/Gelenk |  |  |  |  |  |  |  | Habs
 | 1 | Zahnriemenscheibe T5, 14 Zähne (d=22,48) | Zahnrad klein zwischenwelle |  |  |  |  |  |  |  | 0
 | 1 | Zahnriemenscheibe T5, 15 Zähne (d=23,87) | Ritzel Motor |  |  |  |  |  |  |  | Habs
 | 1 | Zahnriemenscheibe T5, 48 Zähne (d=76,39) | Zahnrad für Zwischenwelle (514mm) |  |  |  |  |  |  |  | Habs
 | 1 | NEMA 24 - 60x60x57 - 1.9Nm - 6,35mm Achse - 1.4A - 2.ST6018M2008 | Motor |  |  |  |  |  |  |  | -
Schulter | 4 | Zylinderkopfschraube Innensechskant M2 6mm | Sensor Befestigung |  |  |  |  |  |  |  | Habs
 | 1 | Rotary Sensor | Sensor |  |  |  |  |  |  |  | Habs
 | 2 | Unterlegscheiben M2 Dicke 0,5mm | Sensor befestigung |  |  |  |  |  |  |  | Habs
 | 2 | Rillenkugellager 4 x13 x 5 mm | Riemenspanner |  |  |  |  |  |  |  | Habs
 | 4 | Rillenkugellager 4 x13 x 5 mm mit Flansch | Riemenspanner |  |  |  |  |  |  |  | Habs
 | 40 | Rohr 4mmx3.1mm (=M3) | Riemenspanner |  |  |  |  |  |  |  | -
 | 4 | Unterlegscheiben M3 Kunststoff 0,8mm, Außendurchmesser 7mm | Riemenspanner |  |  |  |  |  |  |  | Habs
 | 4 | Vierkant Mutter M3 Breite 5.5mm | Riemenspanner |  |  |  |  |  |  |  | Habs
 | 2 | Zylinderkopfschraube Innensechskant M3 20mm | Riemenspanner |  |  |  |  |  |  |  | Habs
 | 3 | Unterlegscheiben M3 Dicke 0,5mm, Außendurchmesser 7mm | Riemenspanner |  |  |  |  |  |  |  | Habs
 | 1 | Zylinderkopfschraube Innensechskant M3 40mm | Riemenspanner |  |  |  |  |  |  |  | Habs
 | 1 | Zylinderkopfschraube Innensechskant M3 45mm | Riemenspanner |  |  |  |  |  |  |  | Habs
 | 1 | Zylinderkopfschraube Innensechskant M3 25mm | Riemenspanner |  |  |  |  |  |  |  | 0
 | 2 | Rillenkugellager 8x22x7 | Zwischenachse |  |  |  |  |  |  |  | Habs
 | 120 | Silberstahlwelle 8mm Durchmesser | Zwischenachse |  |  |  |  |  |  |  | 0
 | 1 | Zahnriemenscheibe T5, 48 Zähne (d=76,39) | Zwischenachse |  |  |  |  |  |  |  | Habs
 | 1 | Zahnriemenscheibe T5, 14 Zähne (d=22,48) | Zwischenachse |  |  |  |  |  |  |  | 0
 | 1 | Zahnriemen T5 450mm 10mm Breite | Riemen Zwischachse/Oberarm |  |  |  |  |  |  |  | Habs
 | 1 | Zahnriemenscheibe T5, 14 Zähne (d=22,48) | MotorRiemenscheibe |  |  |  |  |  |  |  | 0
 | 1 | Zahnriemen T5 340mm 10mm Breite | Motorachse Riemen |  |  |  |  |  |  |  | Habs
 | 4 | Zylinderkopfschraube Innensechskant M3 20mm | Motorbefestigung |  |  |  |  |  |  |  | Habs
 | 4 | Zylinderkopfschraube Innensechskant M3 45mm | Block/Gabel Befestigung |  |  |  |  |  |  |  | Habs
 | 4 | Distanzbolzen 2x Innen M3 20mm, Schlüsselweite 5,5mm | Block/Gabel Befestigung |  |  |  |  |  |  |  | -
 | 300 | Gewindestange M3 | Gabel/Basis Befestigung |  |  |  |  |  |  |  | -
 | 6 | Unterlegscheiben M3 Stahl 0,8mm, Außendurchmesser 9mm | Gabel/Basis Befestigung |  |  |  |  |  |  |  | -
 | 6 | Distanzbolzen 2x Innen M3 20mm, Schlüsselweite 5,5mm | Gabel/Basis Befestigung |  |  |  |  |  |  |  | -
 | 1 | NEMA 24 - 60x60x87 - 3.0Nm - 8mm Achse - 4.0A | Motor |  |  |  |  |  |  |  | -
 | 2 | Rillenkugellager DIN 625 SKF - SKF 61818 - 80x100x10 | Oberarm-Kugellager |  |  |  |  |  |  |  | Habs
Hüfte | 1 | Rillenkugellager DIN 625 SKF - SKF 61818 - 90x115x13 | Hüftdrehgelenk |  |  |  |  |  |  |  | Habs
 | 6 | Zylinderkopfschraube Innensechskant M3 40mm | Gabel/Basis Befestigung |  |  |  |  |  |  |  | Habs
 | 6 | Unterlegscheiben M3 Stahl 0,8mm, Außendurchmesser 9mm | Gabel/Basis Befestigung |  |  |  |  |  |  |  | -
 | 8 | Senkkopfschraube Innensechskant M3 10mm | Befestigung DrehlagerDeckel/Drehlager/Basis |  |  |  |  |  |  |  | Habs
 | 8 | Distanzbolzen 2x Innen M3 20mm, Schlüsselweite 5,5mm | Befestigung DrehlagerDeckel/Drehlager/Basis |  |  |  |  |  |  |  | -
 | 8 | Zylinderkopfschraube Innensechskant M3 30mm | Befestigung DrehlagerDeckel/Drehlager/Basis |  |  |  |  |  |  |  | Habs
 | 1 | Rotary Sensor | Sensor |  |  |  |  |  |  |  | Habs
 | 4 | Zylinderkopfschraube Innensechskant M2 6mm | Sensor Befestigung |  |  |  |  |  |  |  | Habs
 | 4 | Zylinderkopfschraube Innensechskant M3 20mm | Befestigung HüftMotorBasis |  |  |  |  |  |  |  | Habs
 | 4 | Unterlegscheiben M3 Dicke 0,5mm, Außendurchmesser 7mm | Befestigung HüftMotorBasis |  |  |  |  |  |  |  | Habs
 | 2 | Rillenkugellager 4 x13 x 5 mm | RiemenSpanner HüftMotor |  |  |  |  |  |  |  | Habs
 | 4 | Rillenkugellager 4 x13 x 5 mm mit Flansch | RiemenSpanner HüftMotor |  |  |  |  |  |  |  | Habs
 | 24 | Rohr 4mmx3.1mm (=M3) | RiemenSpanner HüftMotor |  |  |  |  |  |  |  | -
 | 8 | Unterlegscheiben M3 Kunststoff 0,8mm, Außendurchmesser 7mm | RiemenSpanner HüftMotor |  |  |  |  |  |  |  | Habs
 | 1 | Zahnriemenscheibe T5, 10 Zähne (d=15,92) | HüftMotor Zahnriemenrad |  |  |  |  |  |  |  | -
 | 1 | Zahnriemen T5 510mm 10mm Breite | Hüftmotor Zahnriemen |  |  |  |  |  |  |  | Habs
 | 1 | NEMA 23 - 57x57x56 - 1,26Nm - 6,35mm Achse - 2.8A | HüftMotor |  |  |  |  |  |  |  | Habs
 | 16 | Rillenkugellager 3x8x3 | Lager Gehäuse/Schulter |  |  |  |  |  |  |  | Habs
 | 1 | Passfeder 2x2x8 DIN 6885 | Motor Well/Nabe Verbindung
Material
 | #VPE | Artikel |  |  |  | VPE | Preis | benötigt | Rest | Summe
 | 0 | Zylinderkopfschraube Innensechskant M3 12mm |  | http://www.amazon.de/Zylinderkopfschrauben-Edelstahl-Zylinderschrauben-Inbusschrauben-Innensechskant/dp/B018XL5XNG |  | 50 | 2.50 € | 0 | 0 | 0.00 € | Habs
 | 0 | Zylinderkopfschraube Innensechskant M3 16mm |  | http://www.ebay.de/itm/191777095007?var=490801405876 |  | 50 | 2.50 € | 0 | 0 | 0.00 € | Habs
 | 1 | Zylinderkopfschraube Innensechskant M3 20mm |  | http://www.ebay.de/itm/191777095007?var=490801405876 |  | 50 | 2.50 € | 44 | 6 | 2.50 € | Habs
 | 1 | Zylinderkopfschraube Innensechskant M3 25mm |  | http://www.ebay.de/itm/191777095007?var=490801405876 |  | 50 | 2.50 € | 7 | 43 | 2.50 € | Habs
 | 1 | Zylinderkopfschraube Innensechskant M3 30mm |  | http://www.ebay.de/itm/191777095007?var=490801405876 |  | 50 | 2.50 € | 20 | 30 | 2.50 € | Habs
 | 0 | Zylinderkopfschraube Innensechskant M3 35mm |  | http://www.ebay.de/itm/191777095007?var=490801405876 |  | 50 | 2.50 € | 0 | 0 | 0.00 € | Bestellt
 | 1 | Zylinderkopfschraube Innensechskant M3 40mm |  | http://www.ebay.de/itm/191777095007?var=490801405876 |  | 50 | 2.50 € | 11 | 39 | 2.50 € | Habs
 | 1 | Zylinderkopfschraube Innensechskant M3 45mm |  | http://www.ebay.de/itm/Senkkopfschrauben-Innensechskant-DIN-7991-M3-Laengen-von-4-bis-45-mm-V2A-A2-/121104449387 |  | 50 | 2.50 € | 14 | 36 | 2.50 € | Habs
 | 1 | Zylinderkopfschraube Innensechskant M2 6mm |  | http://www.ebay.de/itm/191777095007?var=490801405809 |  | 20 | 1.80 € | 20 | 0 | 1.80 € | Habs
 | 1 | Zylinderkopfschraube Innensechskant M2 12mm |  | http://www.ebay.de/itm/191777095007?var=490801405798 |  | 20 | 1.80 € | 4 | 16 | 1.80 € | Habs
 | 1 | Senkkopfschraube Innensechskant M3 10mm |  | http://www.ebay.de/itm/401011184909?var=670540129220 |  | 50 | 2.99 € | 20 | 30 | 2.99 € | Habs
 | 0 | Senkkopfschraube Innensechskant M3 25mm |  | http://www.ebay.de/itm/120518872335 | http://www.amazon.de/St%C3%BCck-Senkkopfschraube-Innensechskant-7991-Edelstahl/dp/B005HO2N2M | 20 | 2.95 € | 0 | 0 | 0.00 € | Habs
 | 1 | Vierkant Mutter M3 Breite 5.5mm |  | https://www.conrad.de/de/vierkantmuttern-m3-din-562-stahl-100-st-toolcraft-109026-109026.html |  | 100 | 2.09 € | 10 | 90 | 2.09 € | Habs
 | 1 | Muttern M3, Schlüsselweite 5.5 mm |  | https://www.conrad.de/de/sechskantmuttern-m3-stahl-verzinkt-100-st-toolcraft-815624-815624.html |  | 100 | 2.09 € | 10 | 90 | 2.09 € | Habs
 | 0 | Muttern M2 |  | on stock |  | 100 | 2.09 € | 0 | 0 | 0.00 € | Habs
 | 1 | Madenschraube M3 16mm |  | http://www.ebay.de/itm/310530719926?var=610168956880 |  | 50 | 4.89 € | 1 | 49 | 4.89 € | Habs
 | 1 | Madenschraube M3 5mm |  | http://www.ebay.de/itm/310530719926?var=610168956880 |  | 50 | 2.29 € | 2 | 48 | 2.29 € | Habs
 | 1 | Unterlegscheiben M3 Dicke 0,5mm, Außendurchmesser 7mm |  | https://www.conrad.de/de/unterlegscheiben-innen-durchmesser-32-mm-m3-din-125-stahl-verzinkt-100-st-toolcraft-814628-814628.html |  | 100 | 1.79 € | 7 | 93 | 1.79 € | Habs
 | 1 | Unterlegscheiben M2 Dicke 0,5mm |  | https://www.conrad.de/de/unterlegscheiben-innen-durchmesser-22-mm-m2-din-125-stahl-verzinkt-100-st-toolcraft-a22-d125a2k-194696-521659.html |  | 100 | 1.79 € | 4 | 96 | 1.79 € | Habs
 | 0 | Unterlegscheiben 8mm Innendurchmesser |  | Baumarkt |  | 50 | 4.33 € | 0 | 0 | 0.00 € | -
 | 2 | Unterlegscheiben M3 Kunststoff 0,8mm, Außendurchmesser 7mm |  | https://www.conrad.de/de/unterlegscheiben-innen-durchmesser-32-mm-m3-din-125-kunststoff-10-st-toolcraft-800281-800281.html |  | 10 | 1.98 € | 12 | 8 | 3.96 € | Habs
 | 0 | Unterlegscheiben M3 Kunststoff 0,8mm, Außendurchmesser 9mm |  | https://www.conrad.de/de/unterlegscheiben-innen-durchmesser-32-mm-m3-din-9021-kunststoff-100-st-toolcraft-32-d9021-poly-194730-521735.html |  | 10 | 1.98 € | 0 | 0 | 0.00 € | Habs
 | 0 | Unterlegscheiben M3 0,8mm, Außendurchmesser 9mm |  | https://www.conrad.de/de/unterlegscheiben-innen-durchmesser-32-mm-m3-din-9021-stahl-verzinkt-100-st-toolcraft-32-d9021a2k-194723-521800.html |  | 10 | 1.98 € | 0 | 0 | 0.00 € | Habs
 | 1 | Silberstahlwelle 6mm Durchmesser |  | https://www.conrad.de/de/silberstahl-welle-500-mm-6-mm-237086.html |  | 500 | 4.49 € | 40 | 460 | 4.49 € | Habs
 | 1 | Silberstahlwelle 3mm Durchmesser |  | https://www.conrad.de/de/silberstahl-welle-500-mm-3-mm-237051.html |  | 500 | 2.49 € | 168 | 332 | 2.49 € | Habs
 | 1 | Silberstahlwelle 8mm Durchmesser |  | https://www.conrad.de/de/silberstahl-welle-500-mm-8-mm-237205.html |  | 500 | 4.49 € | 192 | 308 | 4.49 € | Habs
 | 1 | Rohr 4mmx3.1mm (=M3) |  | https://www.conrad.de/de/silberstahl-welle-500-mm-8-mm-237205.html |  | 500 | 4.49 € | 144 | 356 | 4.49 € | Habs
 | 1 | Unterlegscheiben M3 Stahl 0,8mm, Außendurchmesser 9mm |  | https://www.conrad.de/de/unterlegscheiben-innen-durchmesser-32-mm-m3-din-9021-stahl-verzinkt-100-st-toolcraft-32-d9021a2k-194723-521800.html |  | 100 | 1.59 € | 12 | 88 | 1.59 € | Habs
 | 35 | Distanzbolzen 2x Innen M3 20mm, Schlüsselweite 5,5mm |  | https://www.conrad.de/de/abstandsbolzen-2-x-innengewinde-m3-messing-abstandsmass-20-mm-ii-ms-3-55-20-1-st-526533.html |  | 1 | 0.30 € | 35 | 0 | 10.50 € | Habs
 | 0 | Distanzbolzen M3 5mm, Schlüsselweite 5,5mm |  | https://www.conrad.de/de/pb-fastener-10er-set-abstandsbolzen-5-mm-stahl-verzinkt-m3-10-st-521624.html |  | 10 | 2.09 € | 0 | 0 | 0.00 € | Habs
 | 1 | Gewindestange M3 |  | https://www.conrad.de/de/reely-stahl-gewindestange-500-mm-m3-stahl-237094.html |  | 500 | 1.69 € | 300 | 200 | 1.69 € | Habs
 | 1 | Passfeder 2x2x8 DIN 6885 |  | http://www.agrolager.de/product_info.php?products_id=40002800 |  | 1 | 0.45 € | 1 | 0 | 0.45 € | Habs
 | 0 | Zahnriemenscheibe T2,5, 12 Zähne (d=9,55) |  | http://www.cncshop.at/index.php?a=10117 |  | 1 | 4.96 € | 0 | 0 | 0.00 € | -
 | 1 | Zahnriemenscheibe T2,5, 14 Zähne (d=9,55) |  | http://www.cncshop.at/index.php?a=10117 |  | 1 | 4.96 € | 1 | 0 | 4.96 € | -
 | 1 | Zahnriemenscheibe T2,5, 15 Zähne (d=11,94) |  | http://www.cncshop.at/index.php?a=10119 |  | 1 | 5.10 € | 1 | 0 | 5.10 € | -
 | 0 | Zahnriemenscheibe T2,5, 16 Zähne (d=12,73) |  | http://www.cncshop.at/index.php?a=10120& |  | 1 | 5.10 € | 0 | 0 | 0.00 € | Habs
 | 0 | Zahnriemenscheibe T2,5, 18 Zähne (d=14,32) |  | http://www.cncshop.at/index.php?a=10117 |  | 1 | 4.96 € | 0 | 0 | 0.00 € | -
 | 0 | Zahnriemenscheibe T2,5, 20 Zähne (d=15,92) |  | http://www.cncshop.at/index.php?a=10123 |  | 1 | 4.54 € | 0 | 0 | 0.00 € | Habs
 | 0 | Zahnriemenscheibe T2,5, 22 Zähne (d=17,51) |  | http://www.cncshop.at/index.php?a=10124 |  | 1 | 4.54 € | 0 | 0 | 0.00 € | Habs
 | 0 | Zahnriemenscheibe T2,5, 24 Zähne (d=19,1) |  | http://www.cncshop.at/index.php?a=10125 |  | 1 | 4.54 € | 0 | 0 | 0.00 € | Habs
 | 0 | Zahnriemenscheibe T2,5, 30 Zähne (d=23,87) |  | http://www.cncshop.at/index.php?a=10129 |  | 1 | 5.44 € | 0 | 0 | 0.00 € | Habs
 | 0 | Zahnriemenscheibe T2,5, 32 Zähne (d=23,87) |  | http://www.cncshop.at/index.php?a=10130 |  | 1 | 5.44 € | 0 | 0 | 0.00 € | Habs
 | 0 | Zahnriemenscheibe T2,5, 36 Zähne (d=57,30) |  | http://www.cncshop.at/index.php?a=10067 |  | 1 | 5.44 € | 0 | 0 | 0.00 € | Habs
 | 0 | Zahnriemenscheibe T2,5, 40 Zähne (d=31,83) |  | http://www.cncshop.at/index.php?a=10132 |  | 1 | 5.44 € | 0 | 0 | 0.00 € | -
 | 0 | Zahnriemenscheibe T2,5, 44 Zähne (d=35,01) |  | http://www.cncshop.at/index.php?a=10133 |  | 1 | 5.44 € | 0 | 0 | 0.00 € | -
 | 0 | Zahnriemenscheibe T2,5, 60 Zähne (d=47,75) |  | http://www.cncshop.at/index.php?a=10135 |  | 1 | 6.34 € | 0 | 0 | 0.00 € | -
 | 1 | Zahnriemenscheibe T5, 10 Zähne (d=15,92) |  | http://www.cncshop.at/index.php?a=10051 |  | 1 | 4.39 € | 1 | 0 | 4.39 € | Habs
 | 0 | Zahnriemenscheibe T5, 12 Zähne (d=19,10) |  | http://www.cncshop.at/index.php?a=10052 |  | 1 | 5.07 € | 0 | 0 | 0.00 € | Habs
 | 3 | Zahnriemenscheibe T5, 14 Zähne (d=22,48) |  | http://www.cncshop.at/index.php?a=10053 |  | 1 | 5.23 € | 3 | 0 | 15.69 € | Habs
 | 1 | Zahnriemenscheibe T5, 15 Zähne (d=23,87) |  | http://www.cncshop.at/index.php?a=10054 |  | 1 | 5.23 € | 1 | 0 | 5.23 € | Habs
 | 0 | Zahnriemenscheibe T5, 16 Zähne (d=25,46) |  | http://www.cncshop.at/index.php?a=10055& |  | 1 | 5.23 € | 0 | 0 | 0.00 € | Habs
 | 0 | Zahnriemenscheibe T5, 18 Zähne (d=28,65) |  | http://www.cncshop.at/index.php?a=10056 |  | 1 | 5.23 € | 0 | 0 | 0.00 € | -
 | 0 | Zahnriemenscheibe T5, 20 Zähne (d=31,83) |  | http://www.cncshop.at/index.php?a=10058 |  | 1 | 6.67 € | 0 | 0 | 0.00 € | -
 | 0 | Zahnriemenscheibe T5, 22 Zähne (d=35,01) |  | http://www.cncshop.at/index.php?a=10059 |  | 1 | 6.67 € | 0 | 0 | 0.00 € | -
 | 2 | Zahnriemenscheibe T5, 48 Zähne (d=76,39) |  | http://www.cncshop.at/index.php?a=10071 |  | 1 | 11.60 € | 2 | 0 | 23.20 € | Habs
 | 1 | Zahnriemen T2,5 120mm 6mm Breite |  | http://www.cncshop.at/index.php?a=10271 |  | 1 | 4.00 € | 1 | 0 | 4.00 € | Habs
 | 1 | Zahnriemen T2,5 145mm 6mm Breite |  | http://www.cncshop.at/index.php?a=10272 |  | 1 | 4.24 € | 1 | 0 | 4.24 € | Habs
 | 0 | Zahnriemen T2,5 160mm 6mm Breite |  | http://www.cncshop.at/index.php?a=10273 |  | 1 | 4.24 € | 0 | 0 | 0.00 € | Habs
 | 0 | Zahnriemen T2,5 177,5mm 6mm Breite |  | http://www.cncshop.at/index.php?a=10274 |  | 1 | 4.00 € | 0 | 0 | 0.00 € | Habs
 | 0 | Zahnriemen T2,5 200mm 6mm Breite |  | http://www.cncshop.at/index.php?a=10275 |  | 1 | 4.44 € | 0 | 0 | 0.00 € | Habs
 | 0 | Zahnriemen T2,5 230mm 6mm Breite |  | http://www.cncshop.at/index.php?a=10276 |  | 1 | 4.96 € | 0 | 0 | 0.00 € | Habs
 | 0 | Zahnriemen T2,5 245mm 6mm Breite |  | http://www.cncshop.at/index.php?a=10277 |  | 1 | 4.96 € | 0 | 0 | 0.00 € | Habs
 | 1 | Zahnriemen T2,5 250mm 6mm Breite |  | http://www.cncshop.at/index.php?a=10276 |  | 1 | 4.96 € | 1 | 0 | 4.96 € | Habs
 | 0 | Zahnriemen T2,5 285mm 6mm Breite |  | http://www.cncshop.at/index.php?a=10279 |  | 1 | 4.00 € | 0 | 0 | 0.00 € | Habs
 | 0 | Zahnriemen T5 295mm 10mm Breite |  | http://www.cncshop.at/index.php?a=10306& |  | 1 | 4.96 € | 0 | 0 | 0.00 € | Habs
 | 0 | Zahnriemen T5 330mm 10mm Breite |  | http://www.cncshop.at/index.php?a=10310 |  | 1 | 4.96 € | 0 | 0 | 0.00 € | Habs
 | 1 | Zahnriemen T5 340mm 10mm Breite |  | http://www.cncshop.at/index.php?a=10311 |  | 1 | 7.13 € | 1 | 0 | 7.13 € | Habs
 | 1 | Zahnriemen T5 375mm 10mm Breite |  | http://www.cncshop.at/index.php?a=10325 |  | 1 | 7.88 € | 1 | 0 | 7.88 € | Habs
 | 1 | Zahnriemen T5 430mm 10mm Breite |  | http://www.cncshop.at/index.php?a=10325 |  | 1 | 7.88 € | 1 | 0 | 7.88 € | Habs
 | 1 | Zahnriemen T5 450mm 10mm Breite |  | http://www.cncshop.at/index.php?a=10325 |  | 1 | 7.88 € | 1 | 0 | 7.88 € | Habs
 | 0 | Zahnriemen T5 480mm 10mm Breite |  | http://www.cncshop.at/index.php?a=10325 |  | 1 | 7.88 € | 0 | 0 | 0.00 € | Habs
 | 0 | Zahnriemen T5 500mm 10mm Breite |  | http://www.cncshop.at/index.php?a=10326 |  | 1 | 7.88 € | 0 | 0 | 0.00 € | Habs
 | 1 | Zahnriemen T5 510mm 10mm Breite |  | http://www.cncshop.at/index.php?a=10327& |  | 1 | 8.87 € | 1 | 0 | 8.87 € | Habs
 | 0 | Zahnriemen T5 560mm 10mm Breite |  | http://www.cncshop.at/index.php?a=10331 |  | 1 | 7.13 € | 0 | 0 | 0.00 € | Habs
 | 0 | NEMA 17 - 42x42x25 - 0,18Nm - 5mm Achse - 0,35A 12V |  | http://www.omc-stepperonline.com/nema-17-bipolar-step-motor-29v-07a-18ncm255ozin-17hs100704s-p-260.html |  | 1 | 14.50 € | 0 | 0 | 0.00 € | Habs
 | 0 | NEMA 17 - 42x42x34 - 0,40Nm - 5mm Achse - 0,40A 12V |  | http://www.omc-stepperonline.com/nema-17-bipolar-stepper-12v-04a-40ncm567ozin-17hs150404s-p-14.html |  | 1 | 14.50 € | 0 | 0 | 0.00 € | Habs
 | 1 | NEMA 17 - 42x42x21 - 0,73Nm - 5mm Achse - 1.2A |  | http://www.omc-stepperonline.com/nema-17-bipolar-step-motor-29v-07a-18ncm255ozin-17hs100704s-p-260.html |  | 1 | 14.50 € | 1 | 0 | 14.50 € | Habs
 | 1 | NEMA 17 - 42x42x34 - 0,26Nm - 5mm Achse - 0.4A 12V - 17HS13-404s |  | http://www.omc-stepperonline.com/nema-17-stepper-motor-34mm-12v-04a-26ncm37ozin-17hs130404s-p-166.html |  | 1 | 8.50 € | 1 | 0 | 8.50 € | Habs
 | 1 | NEMA 24 - 60x60x57 - 1.9Nm - 6,35mm Achse - 1.4A - 2.ST6018M2008 |  | http://de.nanotec.com/produkte/541-st6018-schrittmotor-nema-24/ |  | 1 | 54.20 € | 1 | 0 | 54.20 € | Habs
 | 1 | NEMA 24 - 60x60x87 - 3.0Nm - 8mm Achse - 4.0A |  | http://www.ebay.de/itm/131783082611 |  | 1 | 37.00 € | 1 | 0 | 37.00 € | Habs
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

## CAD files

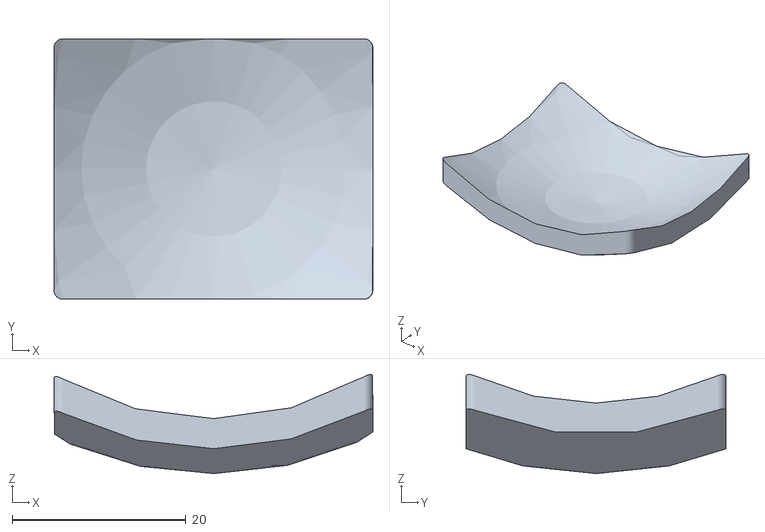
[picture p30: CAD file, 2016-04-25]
3dprint/handgelenk-motordeckel.stl
36.7 x 30.0 x 11.4

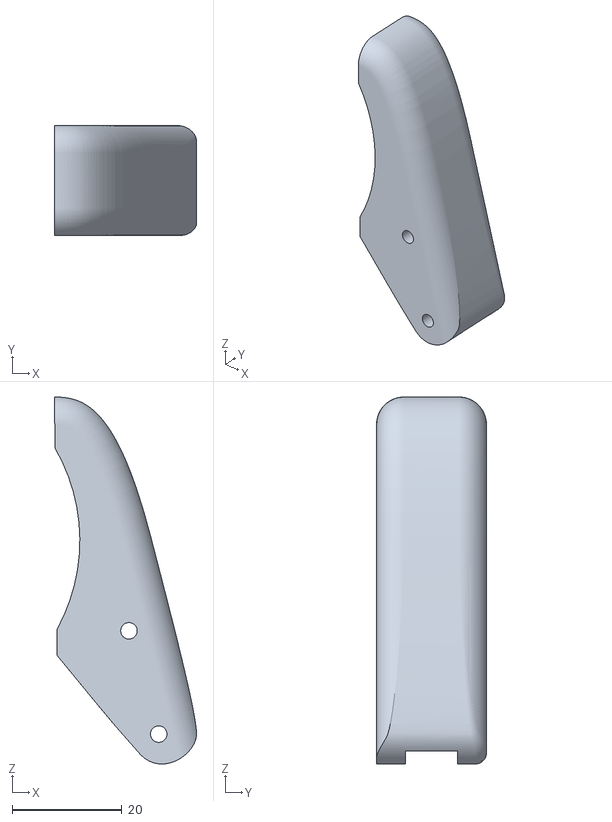
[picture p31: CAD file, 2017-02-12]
cad/simplified/gripper.STL
25.8 x 20.0 x 66.8

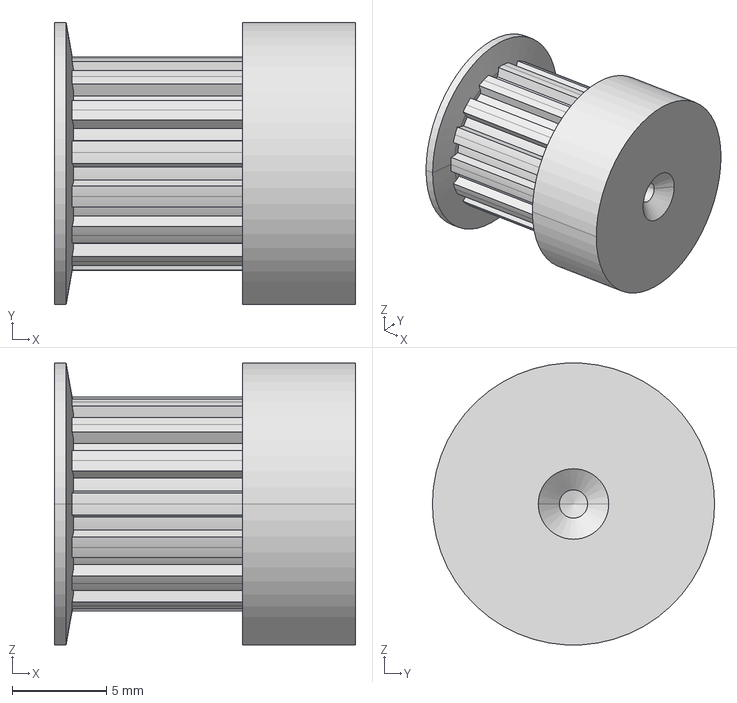
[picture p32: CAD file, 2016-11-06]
cad/symbols/Zahnriemenrad T2.5 15Z.stp
16.0 x 15.0 x 15.0 mm

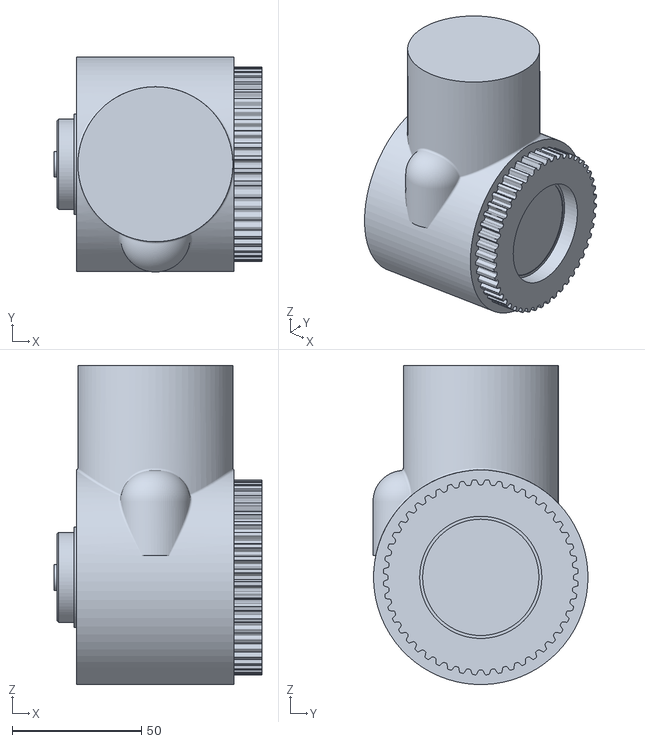
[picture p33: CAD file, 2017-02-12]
cad/simplified/ellbow.stl
80.5 x 83.2 x 123.5

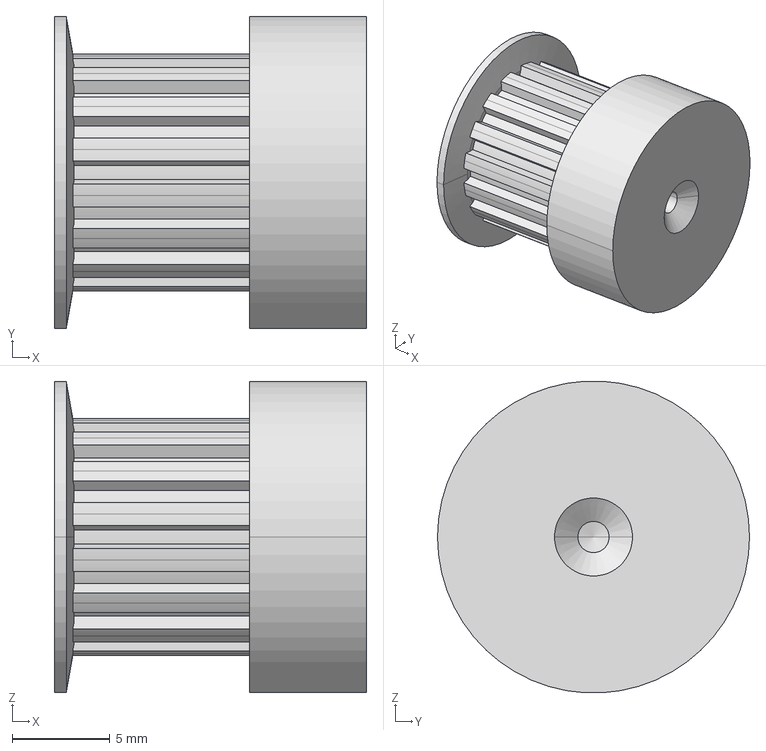
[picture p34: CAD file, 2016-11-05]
cad/symbols/Zahnriemenrad T2.5 16Z.stp
16.0 x 16.0 x 16.0 mm

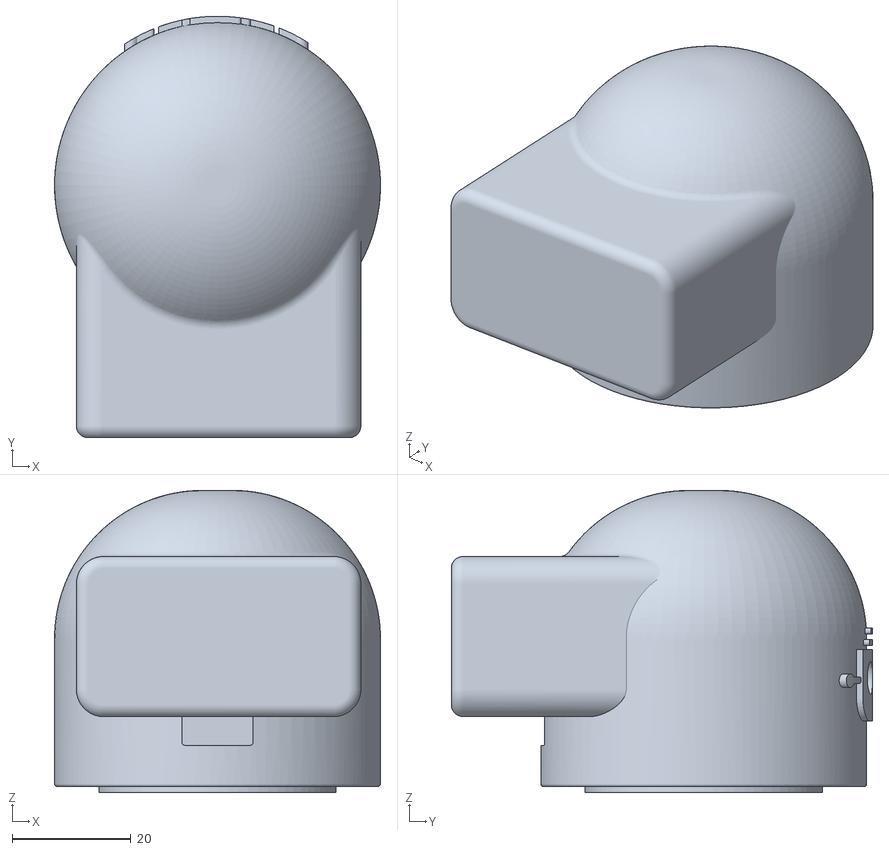
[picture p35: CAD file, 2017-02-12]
cad/simplified/hand.STL
55.0 x 71.1 x 51.0

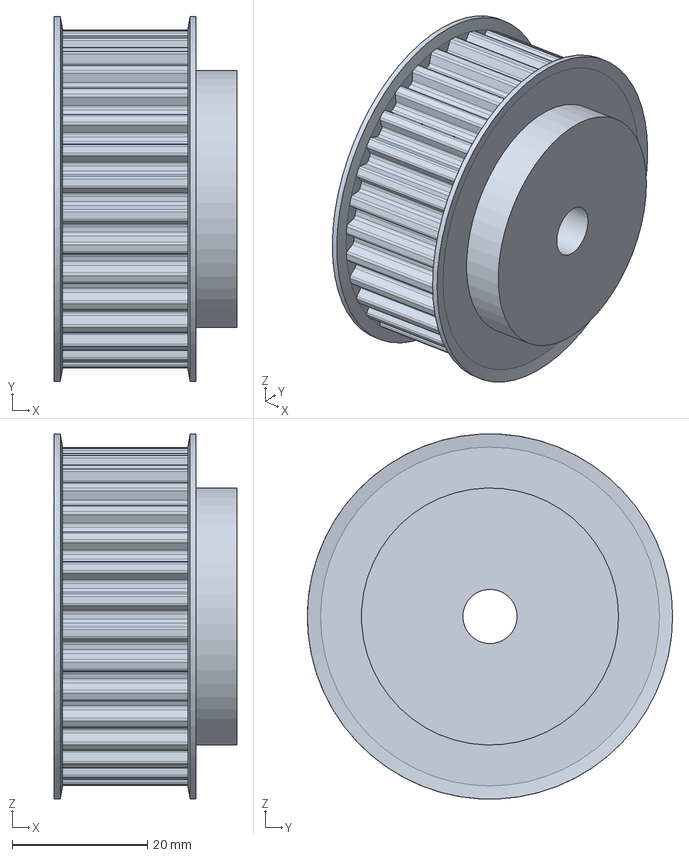
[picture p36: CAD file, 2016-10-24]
cad/symbols/Zahnriemenrad T5 32Z.stp
27.0 x 54.0 x 54.0 mm

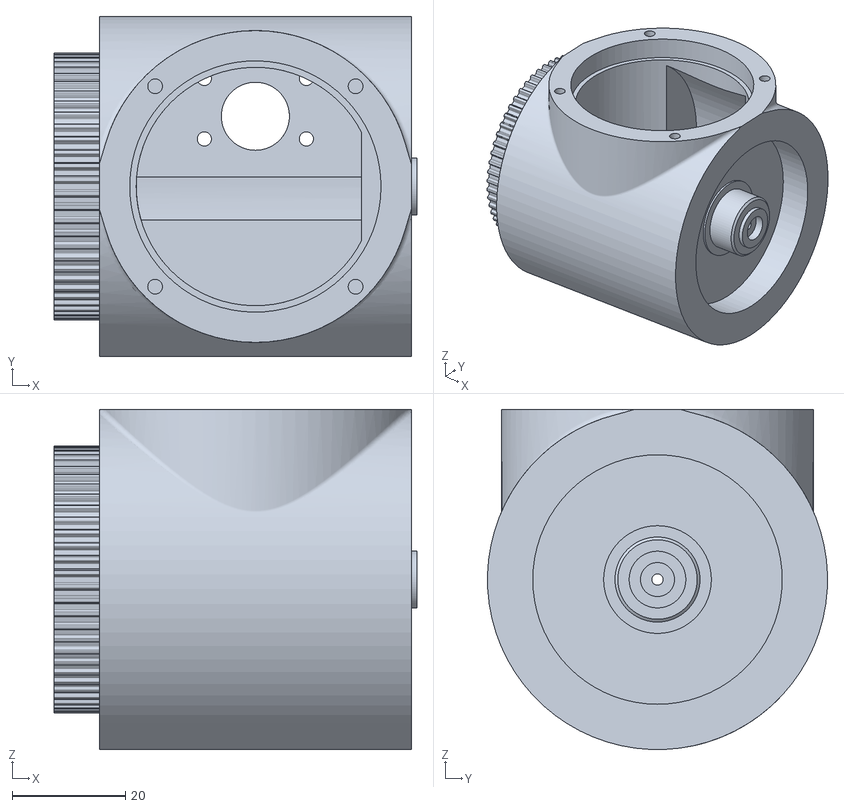
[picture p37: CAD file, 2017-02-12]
cad/simplified/wrist.stl
64.0 x 60.0 x 60.0

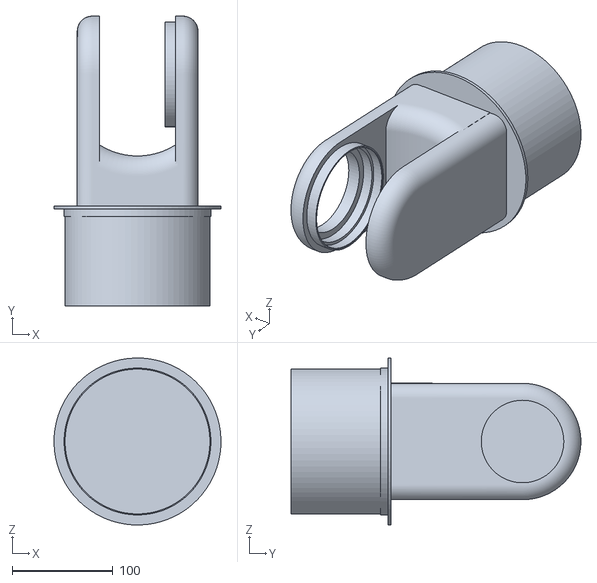
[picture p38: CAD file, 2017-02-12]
cad/simplified/shoulder.STL
166.0 x 287.9 x 166.0

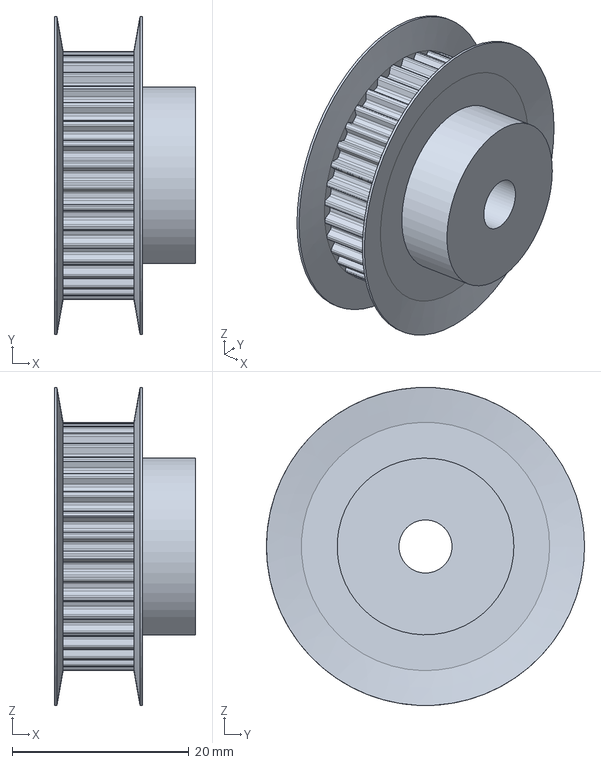
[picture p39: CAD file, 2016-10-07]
cad/symbols/Zahnriemenrad T2.5 36Z.stp
16.0 x 36.0 x 36.0 mm

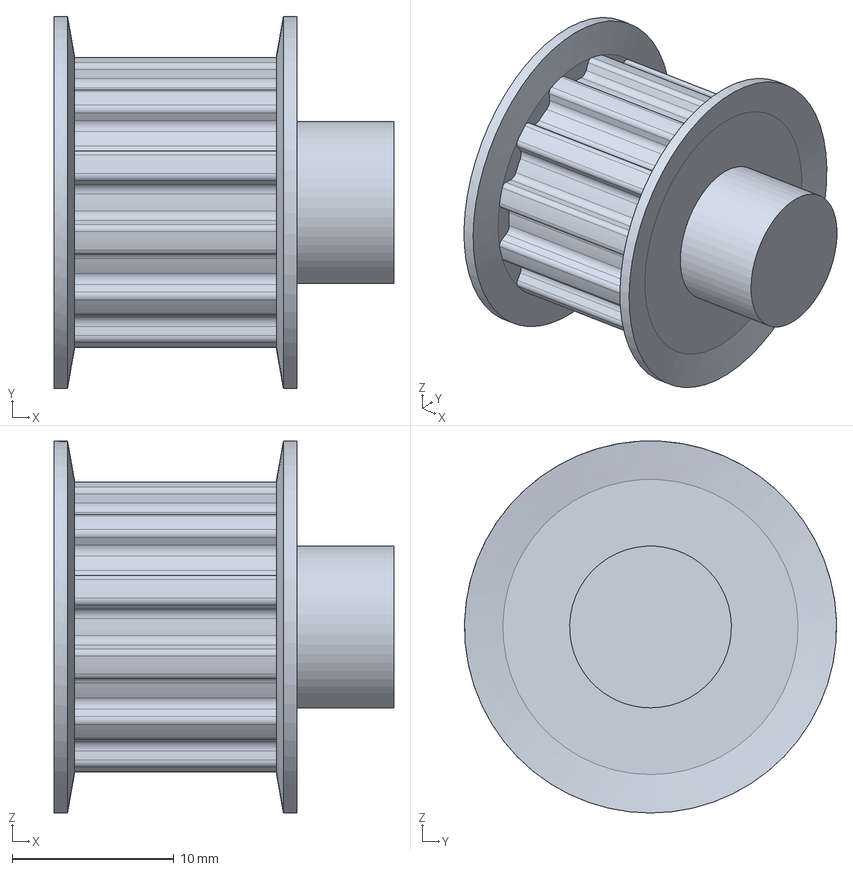
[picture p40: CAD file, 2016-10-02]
cad/symbols/Zahnriemenrad T5 12Z.stp
21.0 x 23.0 x 23.0 mm

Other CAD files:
cad/ellbow-finish.dwg
cad/symbols/Zahnriemenrad T2.5 14Z.stp

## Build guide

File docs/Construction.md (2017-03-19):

Inverse kinematics, i.e. computation of joint angles out of the gripper’s position can be hard. If the design is too playful, nearly impossible complex. So, it is a good idea to ease the maths by having the upper three axes intersecting in one point. Later in the chapter on kinematics we will see that with that limitation kinematics becomes possible without having a mathematician at hand (still not easy, but feasible). 

## Dimensioning 

Before starting the design it is necessary to calculate the torque in all actuators in order to select the steppers and gear ratios properly. In principle, this is simple: The gripper should be able to manipulate 500gr, the forarm has a length of 400mm and the upper arm a length of 350mm, assuming a certain weight per actuator the law of the lever allows to compute the torque of each motor. Tricky part is, that depending on the stepper you choose, the weight of an actuator changes.  In the end I did that computation with excel, and came to these torques 
and gear ratios, which are used to select the stepper's dimensions.

| Actuator | Computed Torque | Gear  | Min Stepper Torque | Selected Stepper Size  | Act. Stepper Torque | 
|--- |---|--- | --- | --- | --- |
| Wrist | 0.6 Nm |  1:4  | 0.18 Nm | NEMA 17 42x42x39 | 0.4 Nm |
| Elbow | 0.6 Nm |  1:7  | 0.11 Nm | NEMA 17 42x42x25 | 0.17 Nm |
| Forearm  | 11 Nm |  1:14 | 0.8 Nm | NEMA 24 60x60x57 | 1.9 Nm |
| Upper arm| 34 Nm |  1:18 | 1.8 Nm | NEMA 24 60x60x87 | 3 Nm |
| Hip | 8 Nm |  1:9  | 0.9 Nm | NEMA 23 57x57x56 | 1.2 Nm |

The steppers are always placed in the previous joint of an actuator in order to move the centre of gravity away from the biggest lever. So, the three heavy steppers actually do not move but turn only when the arm goes up or down.

## Design Patterns

With that amount of torque, shaft-hub joints need to be really stable. While the small steppers have the pulley connected with grub screws, the big ones need something different. Although a lot of filing was involved, I went with feather keys for the middle shaft of gearboxes and the connection between stepper motor and timing pulley.

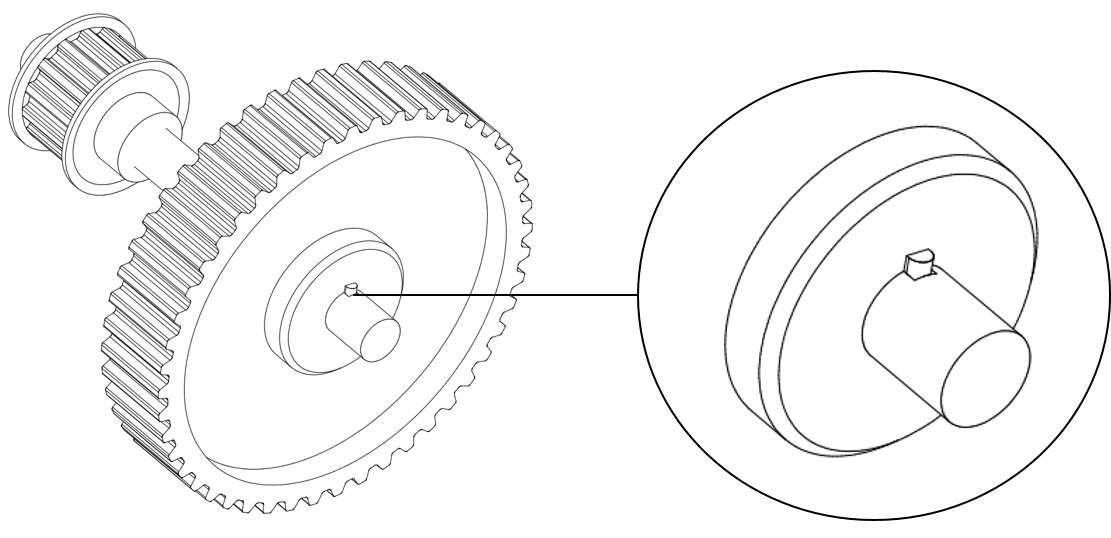
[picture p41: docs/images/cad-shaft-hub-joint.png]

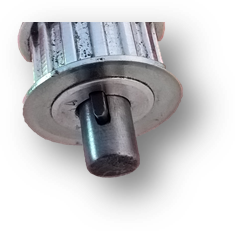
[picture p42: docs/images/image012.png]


## Gripper

Due to space limitations, it seems to be appropriate to use a servo for the gripper. I used a standard design principle where one lever is driven, and the other lever mirrors the movement by a gear wheel. The servo is hidden in a small box, it is a HerkuleX Robot Servo with 0.12 Nm (today I would take the stronger version of the same servo, 0.12Nm is just enough to lift a beer).

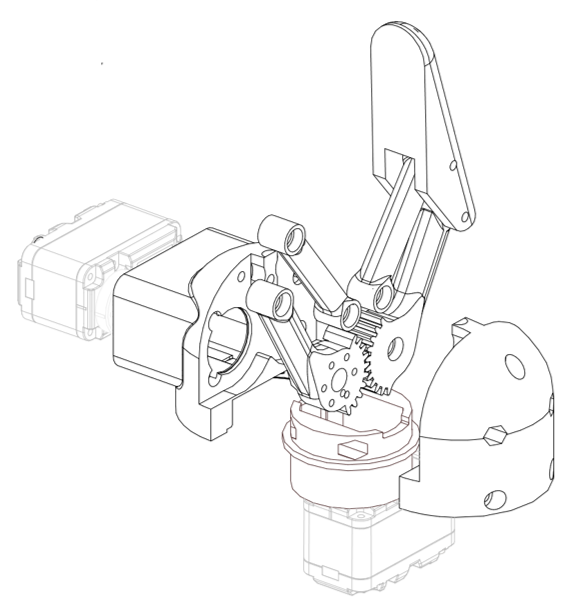
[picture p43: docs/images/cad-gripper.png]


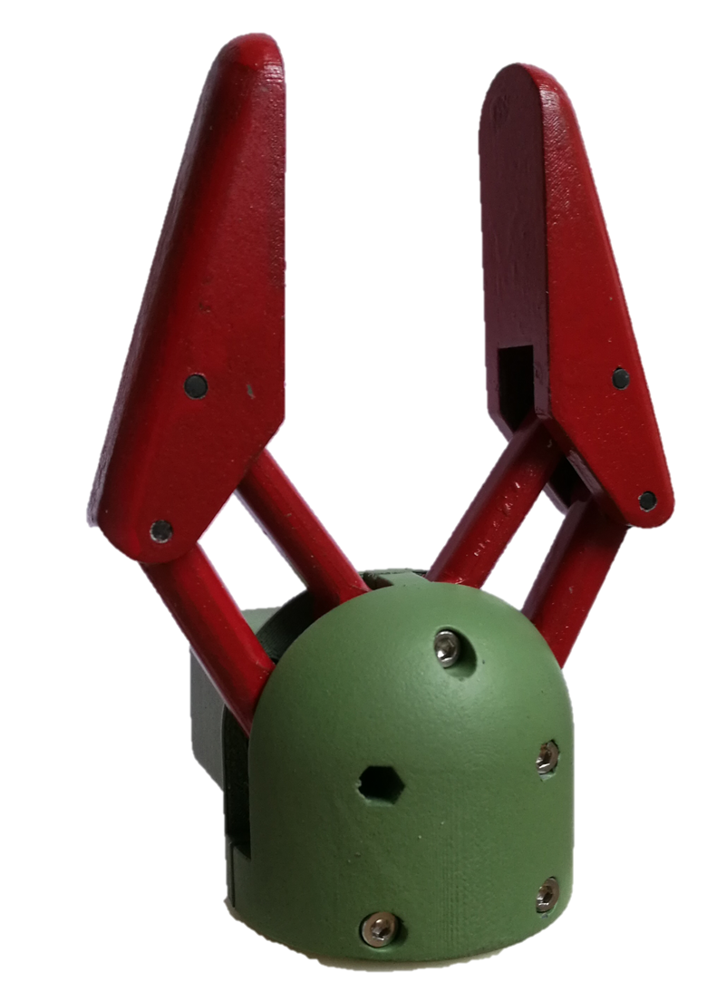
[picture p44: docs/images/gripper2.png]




Assembly has to start from the top, not for mechanical reasons, but due to the cables that are all placed inside the robot going down from the gripper to the base.
The gripper has bearings in all moving parts. The left gearwheel has the servo behind, mounted on the enclosed servo disk. To increase stability, the hole over the servo screw is used for another bearing to lock this lever from both sides in its position.

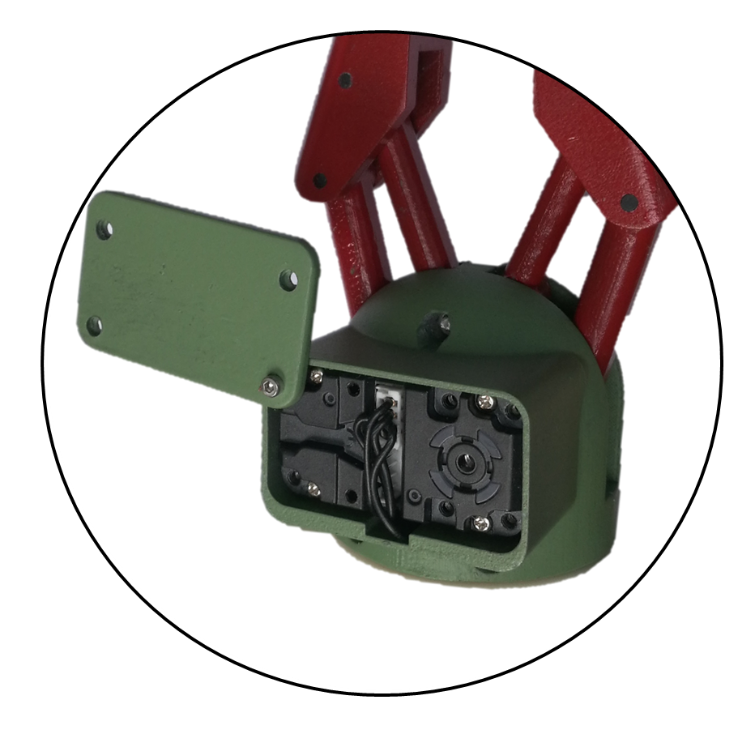
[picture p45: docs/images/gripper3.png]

The servo's cable is going through the servo housing into the flange where the wrist will be placed.

I'm still not really happy with the gripper. Although it works fine, the bulge containing the servo is really ugly. But, the space below the gripper is already occupied by the servo turning the wrist, unfortunately. I played with other design types, but always came back to this one due to its simplicity.

## Wrist

The wrist is also designed with the same servo. A small flange connects the wrist with the two halves of the gripper housing, the hole hides the cable of the gripper servo. Worth to mention is that bearings at both sides of the wrist have a different size, since the servo looks through the inner hole of the bigger bearing. On the other side, in the middle of the smaller bearing there is the hole for the magnet used by the magnetic encoder of the forearm. The cable of both servos (gripper and wrist) is going through the wrist underneath the servo.

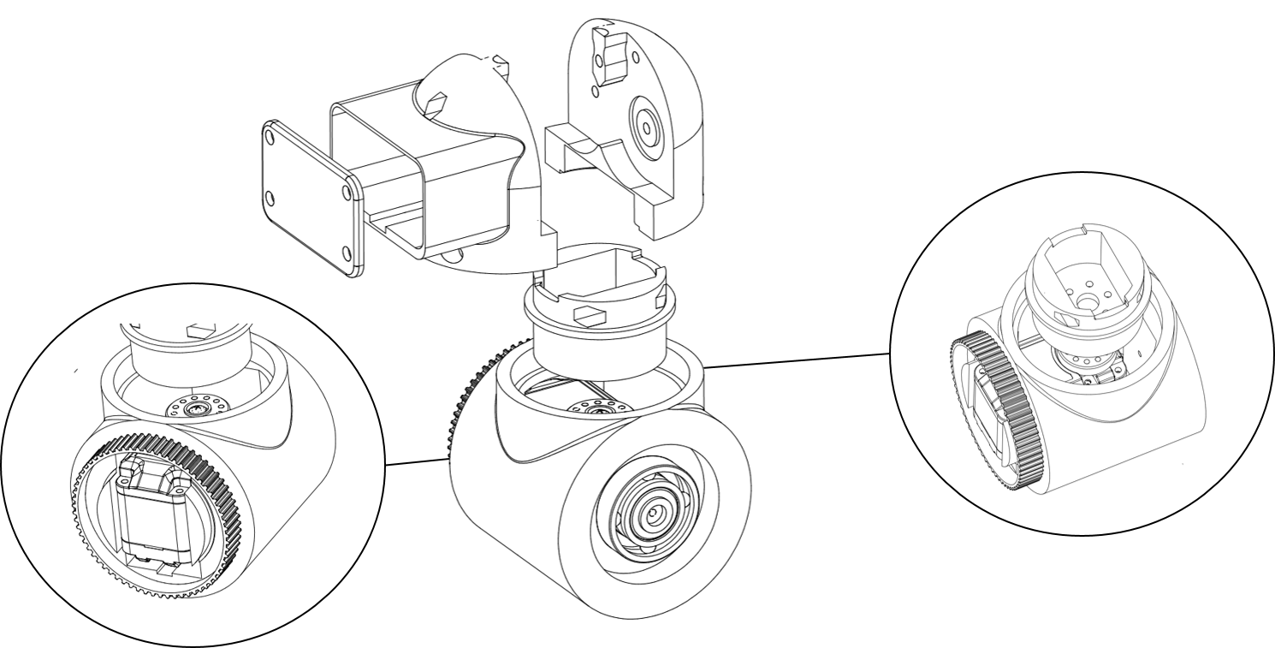
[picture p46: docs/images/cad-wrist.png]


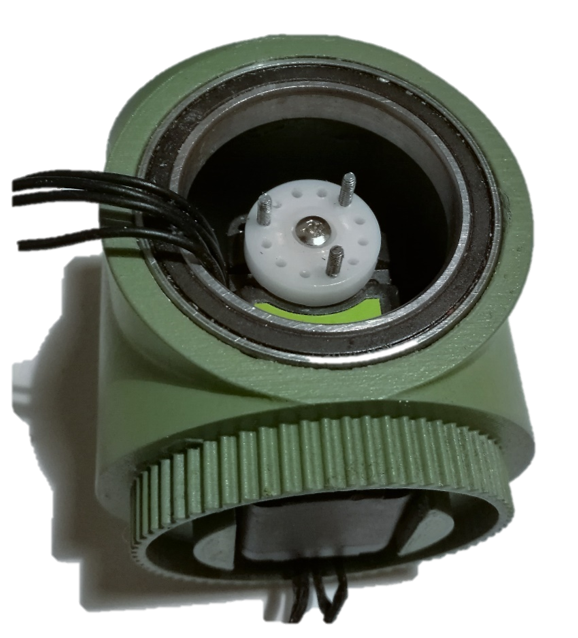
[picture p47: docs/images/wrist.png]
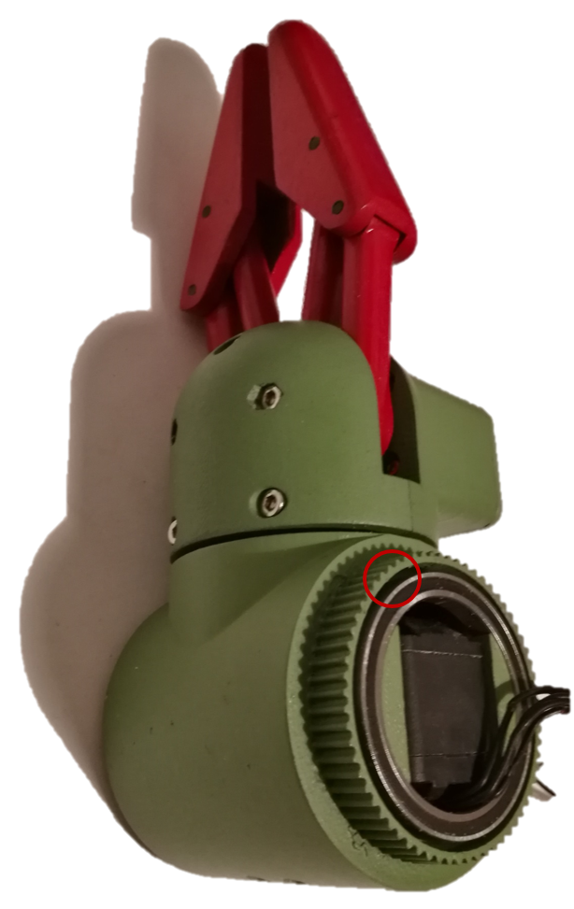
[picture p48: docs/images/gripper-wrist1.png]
The gripper is held with only one extra loose bearing,  since the servo provides the fixed bearing already. The servo is mounted on the back of the wrist with screws. The servohorn is mounted to the flange that links the wrist to the gripper.

The bearing at the right side, that is marked with a red circle is very close to the inner diameter of the belt pulley. This space is occupied by the forearm to fix the bearing with a thin ring. The ring can be seen on the following CAD drawing, also marked with a red circle.

## Forearm

The forearm is more complex, since it drives the wrist with a belt drive and a stepper motor. The belt drive has a gear ratio of 1:4. It is held tight with a spanner. At the other side of the wrist, the magnetic encoder is located. All cables are meeting in the room below the stepper at the bottom, and going down through the hole of the disk.

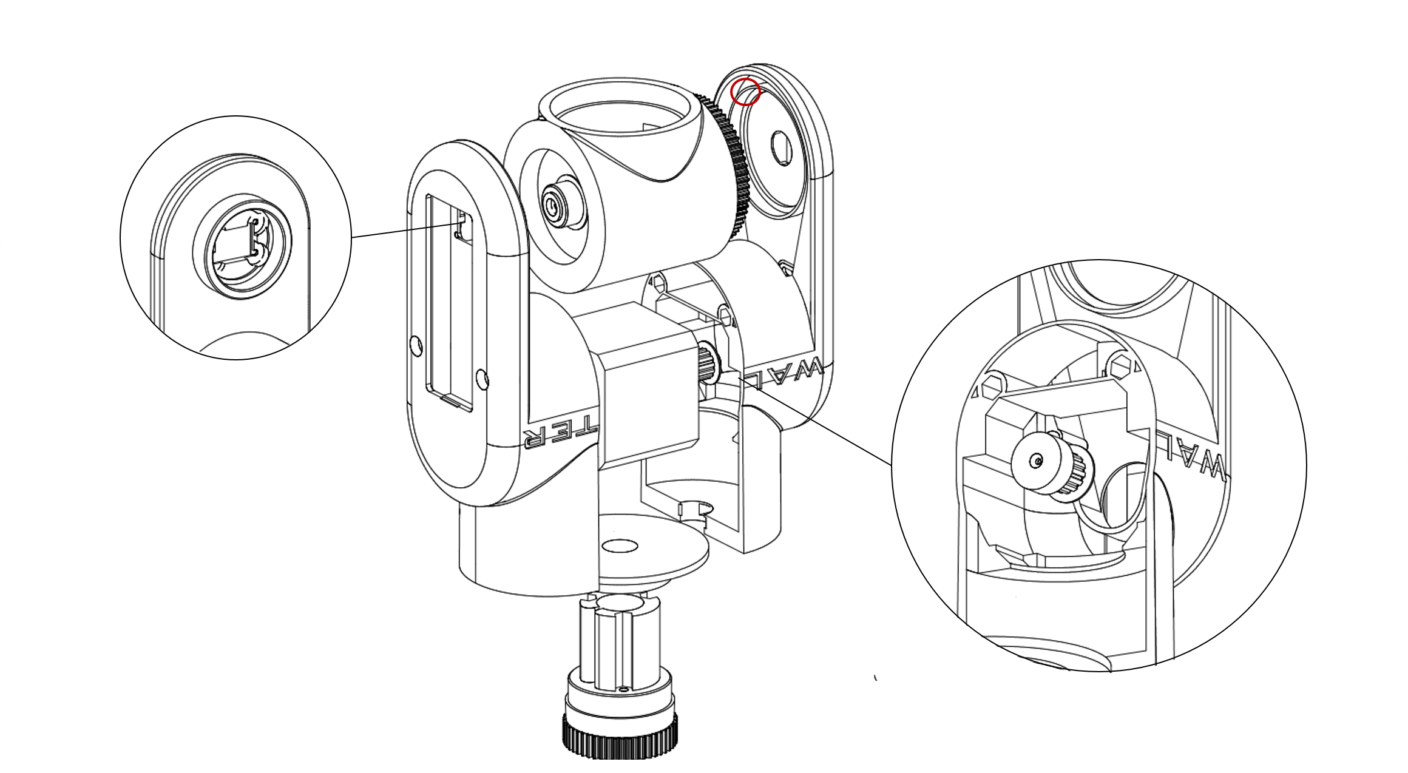
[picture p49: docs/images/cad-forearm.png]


Below, the magnet in the middle of the wrist's bearing can be seen, which has a distance of 1mm to the magnetic encoder of the other half of the forearm.

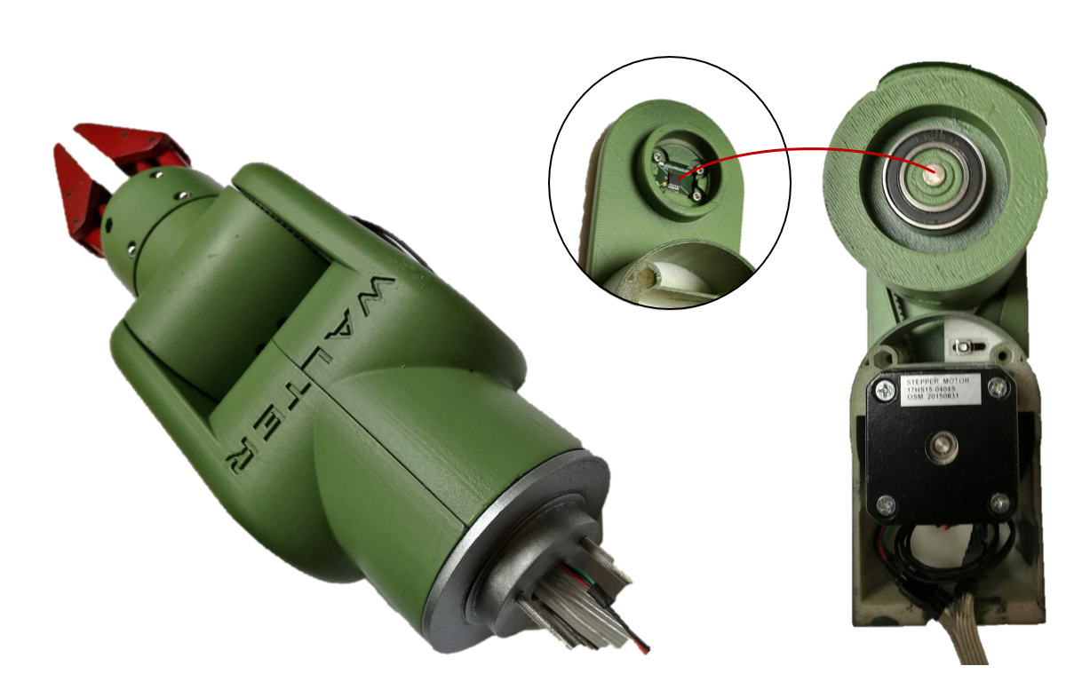
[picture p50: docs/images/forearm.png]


## Elbow

The elbow consumed most design-time, it is a two stage belt-drive with a ratio of 1:7 and a stepper with 17Ncm. The flange in the middle is the connection to the forearm. It is mounted with two  bigger bearings and has a cable channel that gives space to a self made cable drag chain that allows to have the cables inside, since the centre of the axis is occupied by the encoder already.

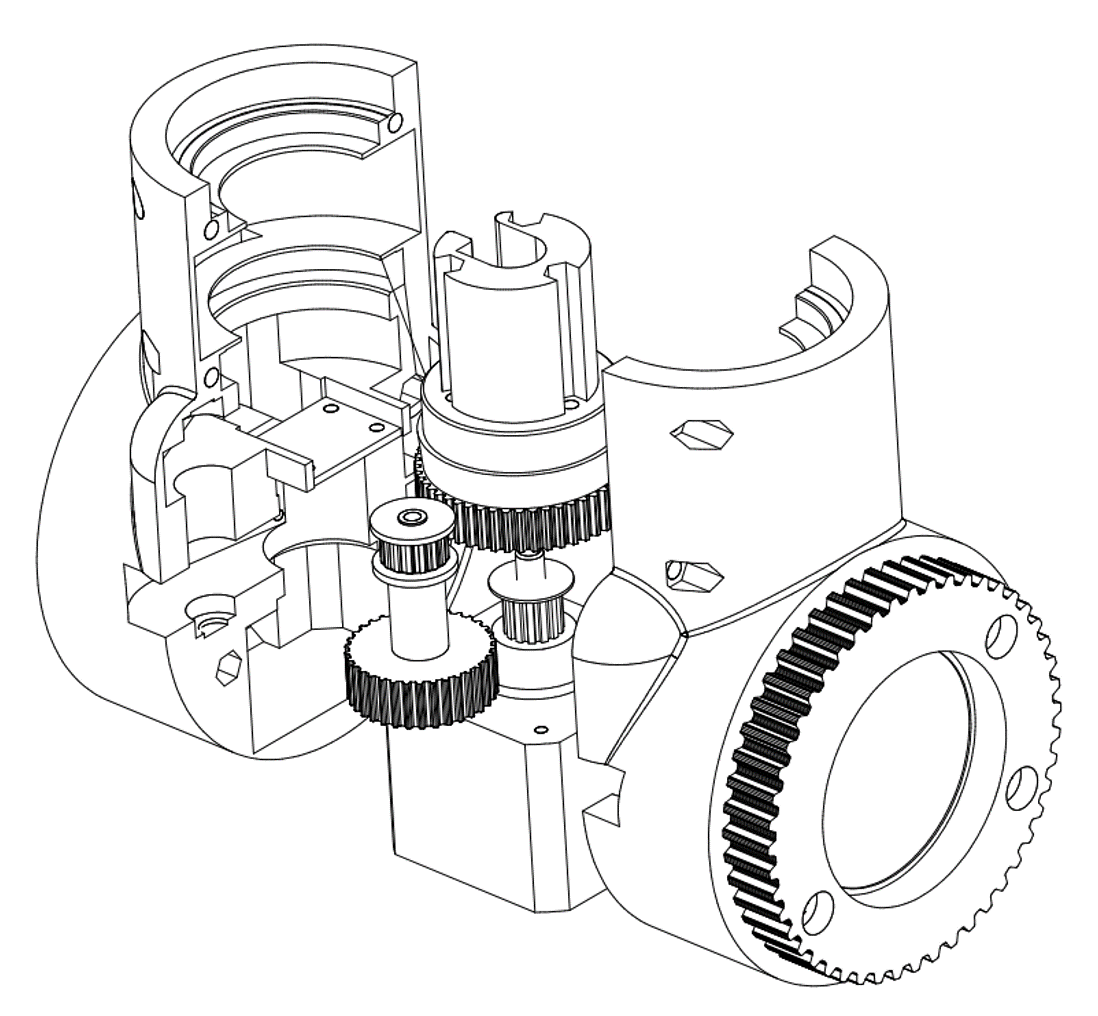
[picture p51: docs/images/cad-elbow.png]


This picture shows the inner construction and the cable drag chain. The magnet in the centre of the flange is right opposite to the encoder, the small PCB in the middle of the ellbow.


At first, I tried to hide the belt pulley within the enclosure, but later on I got the impression that a peep hole exposing a pulley moving faster than the elbow could be a nice technical touch.



## Upper Arm

The upper arm contains a strong stepper with 1.9Nm and a two-staged gear with a ratio of 1:14. On the left side a magnetic encoder samples the angle of the ellbow, above the encoder and the cable channel is located. The cables are going down through a hole in the middle block down to the left side of the bttom part. The ride side contains the belt to the elbow. All belts are tighened with a clamp that can be adjusted from outside.

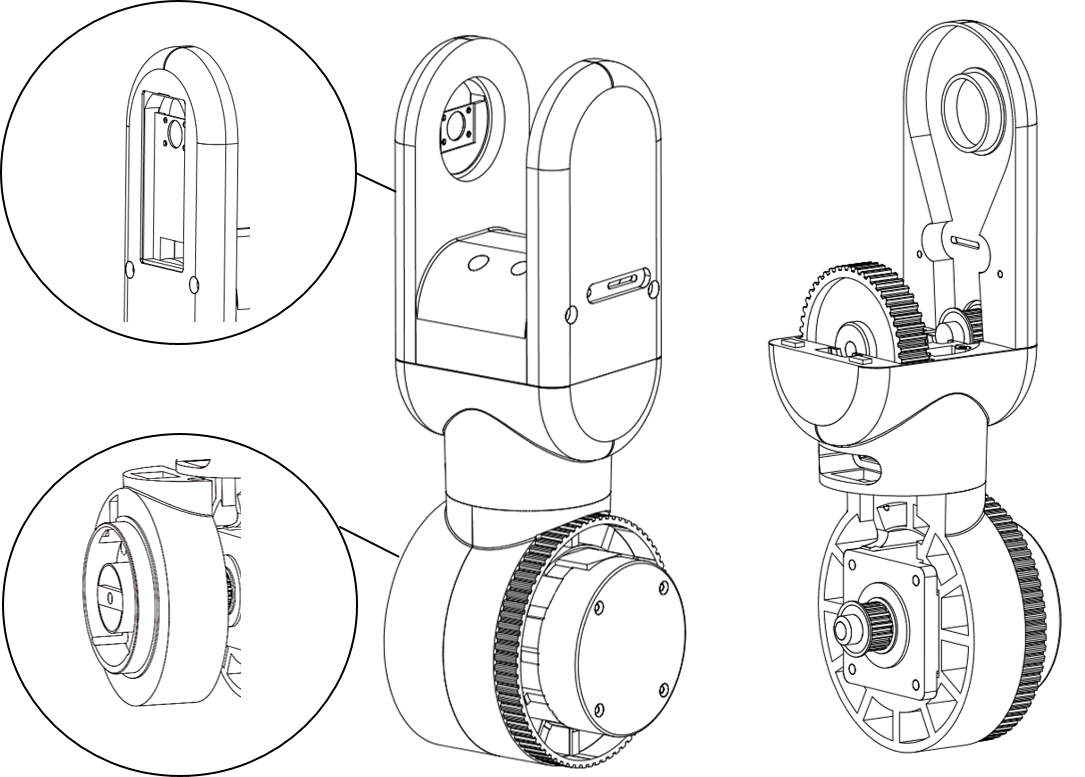
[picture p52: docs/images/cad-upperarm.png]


The cable is going through the centre of the axis. Below the fork of the upper arm, the gearbox is placed.



Right above the belt pinion of the stepper, the magnet for the encoder is placed, in the middle of the space intended for the cables. The thin space between the bearing and the housing will be required by the shoulder actuator to hold the upper arm.
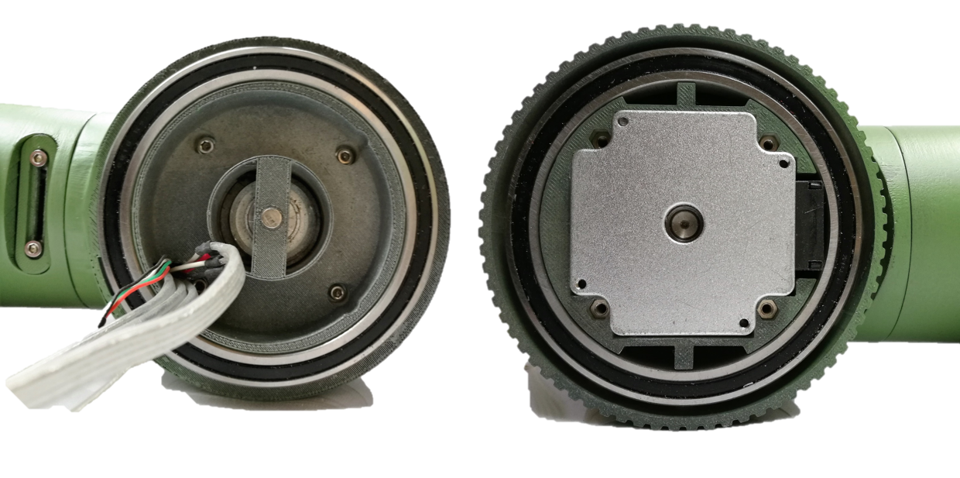
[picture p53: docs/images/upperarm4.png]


## Shoulder

The shoulder contains the strongest stepper moving the upper arm with approx. 3 Nm. A gear ratio of 1:18 could deliver 50Nm, but this number is rather theoretical, since 3D-printed parts would not survive this. But, this allows to reduce the current and use micro-stepping improving the movement.

On the left flange, there is a segment-shaped cable channel below the location of the magnetic encoder. The right flange has a big hole to make room for the stepper's backside. This is hidden by a lid that rotates with the upper arm, which gives a nice technical touch. Inside the middle block between the flanges, there is a shaft with two drive pulleys for the two-staged gearbox, same construction as in the upper arm.

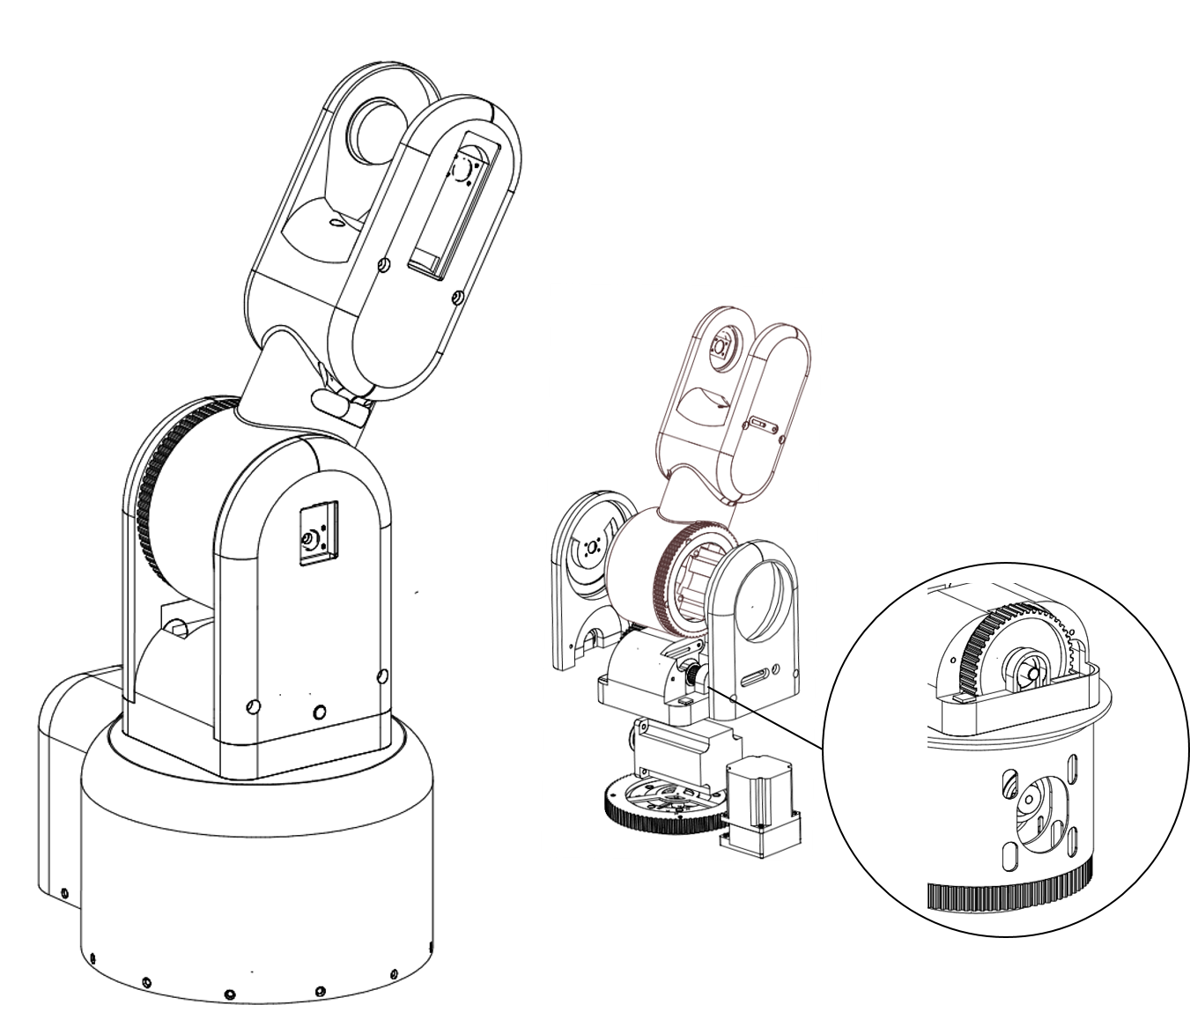
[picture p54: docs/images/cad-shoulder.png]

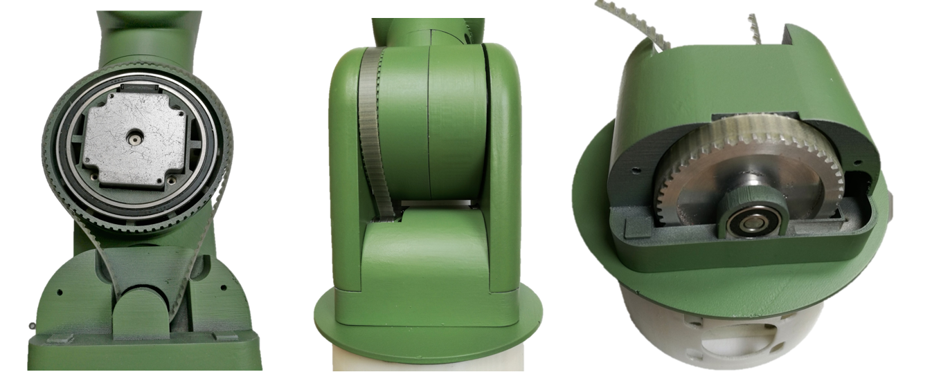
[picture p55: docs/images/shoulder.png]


## Hip

Finally, the hip stepper is what makes the housing of the shoulder look like an iglu. It is a simple belt drive to the shoulder. The shoulder is residing on a drive pulley disk that is mounted on a big bearing.

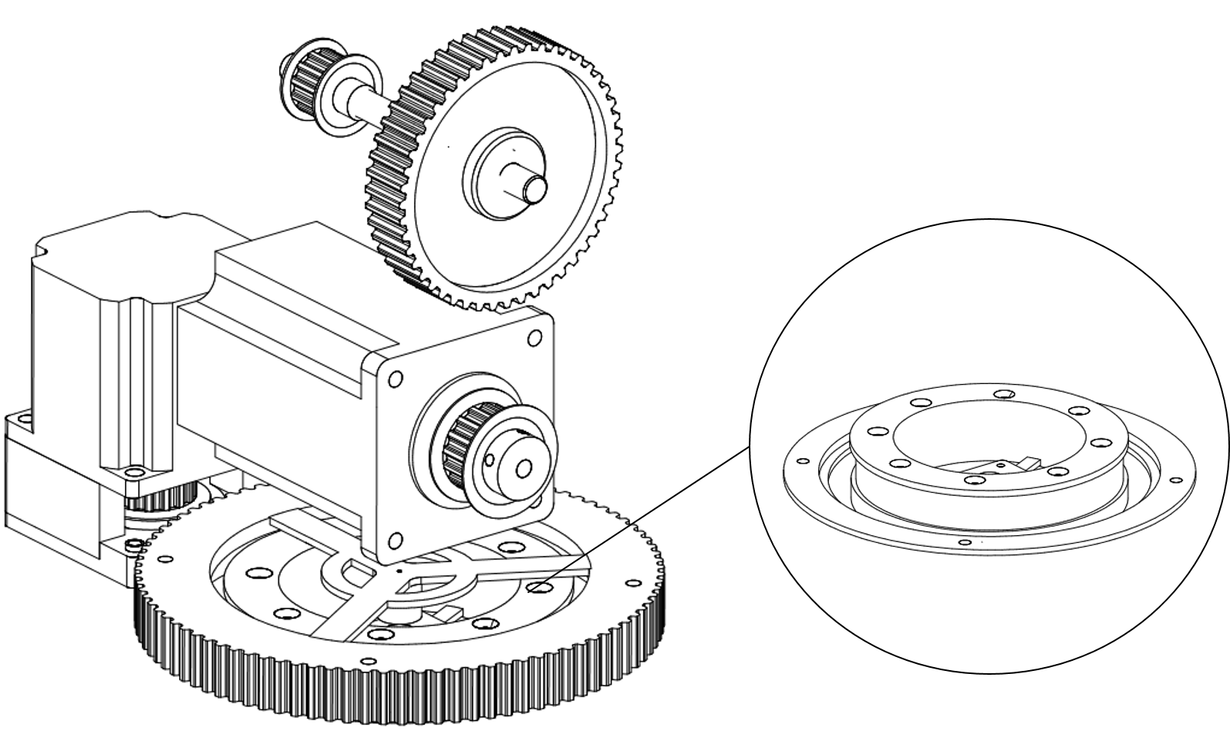
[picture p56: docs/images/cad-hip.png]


The encoder is mounted within the inner base, the magnet is mounted at the outer belt wheel, in between is a big bearing.

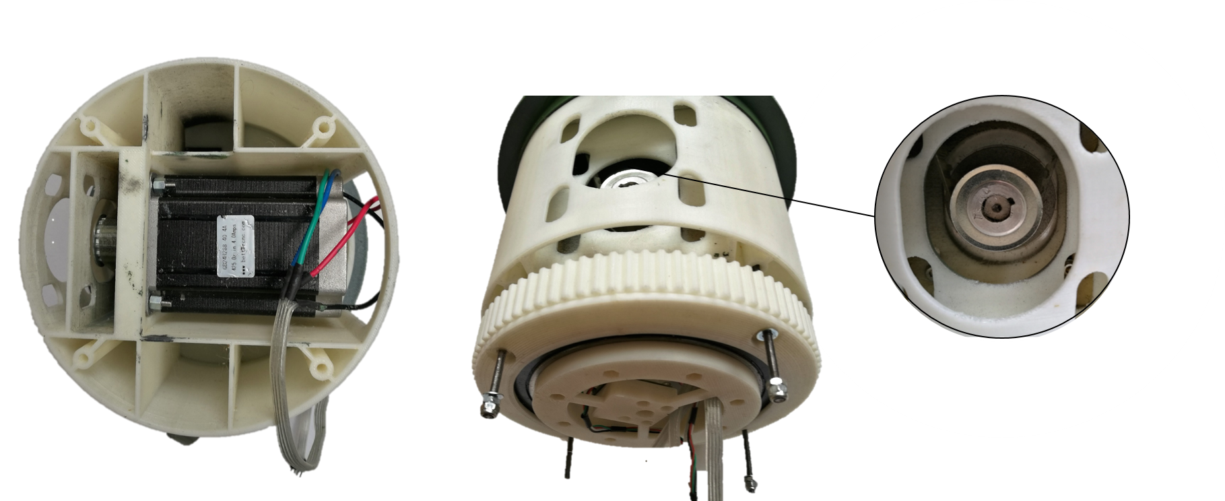
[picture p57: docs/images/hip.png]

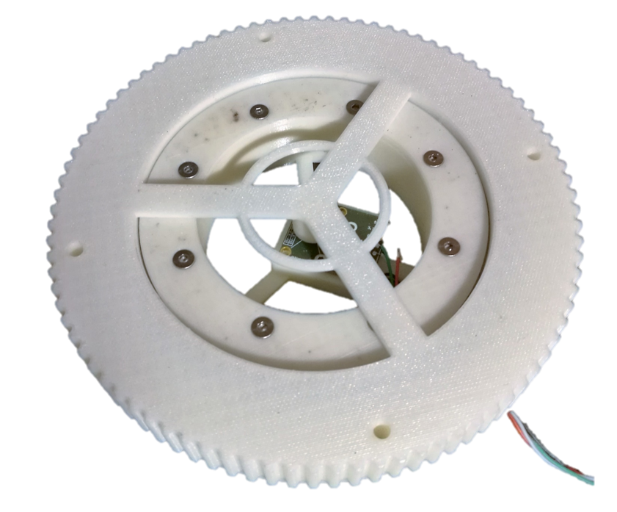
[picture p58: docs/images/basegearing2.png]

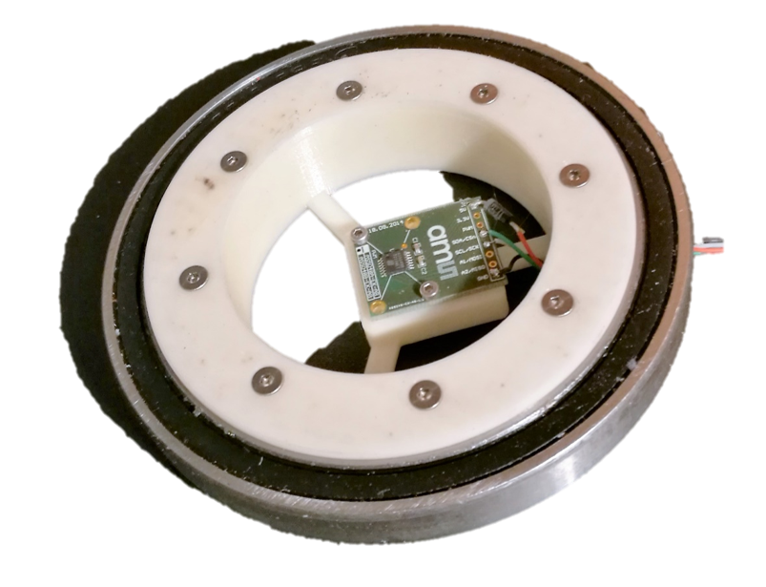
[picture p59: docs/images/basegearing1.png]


## Housing

The housing of the shoulder is not only to hide the hip stepper, but also to stabilize the shoulder by having lots of small bearings on the top edge supporting the shoulder. The inner compartments of the flower pot is filled with iron grain, which has a mass of approx 5kg

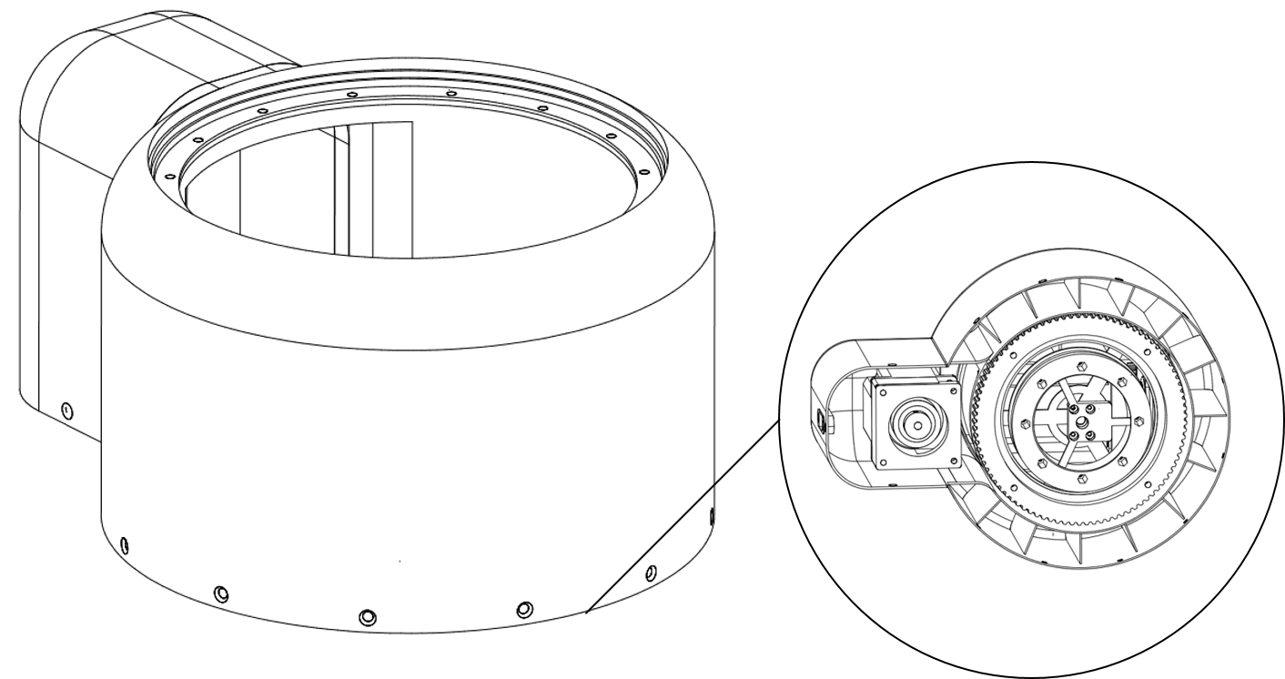
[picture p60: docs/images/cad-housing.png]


The middle layer of the pot is not printed but made of wood for stability reasons. Besides that, I like the look of birch plywood:

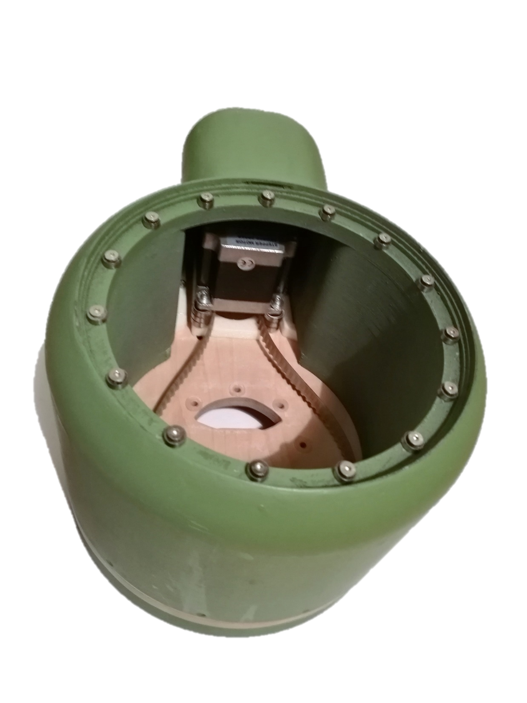
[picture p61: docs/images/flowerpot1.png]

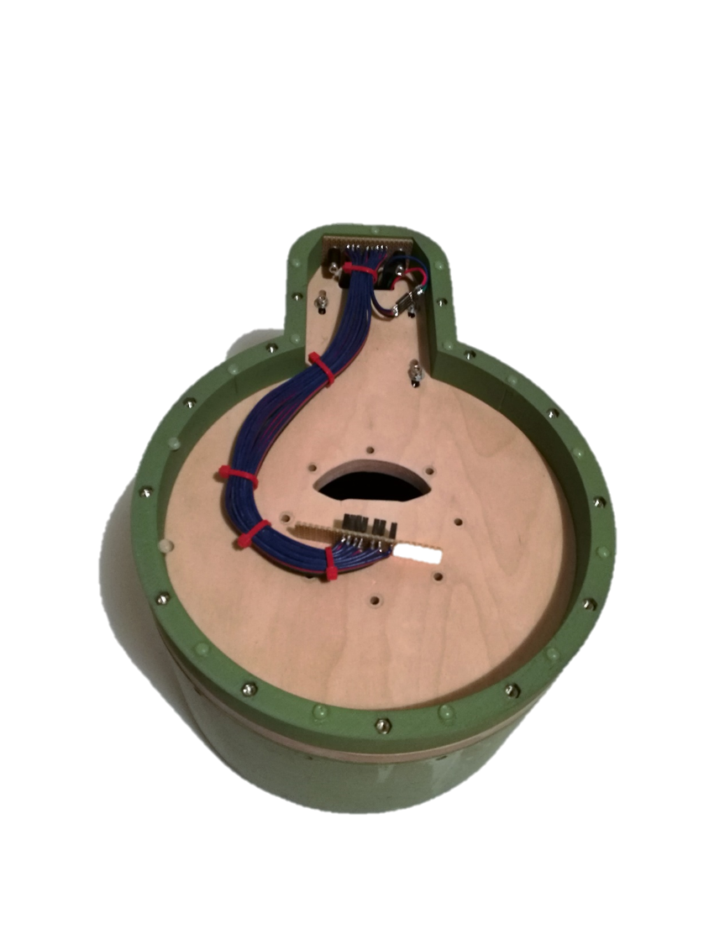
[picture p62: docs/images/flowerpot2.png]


## Cable

Last but not least, a beautiful cable sleeve accompagnies Walter's color. Since all electronics is in the control cabinet, the cable has 5x4 pins for the steppers, 4 pins for the servo's serial connection and 2x 4 pins for the two I2C busses.

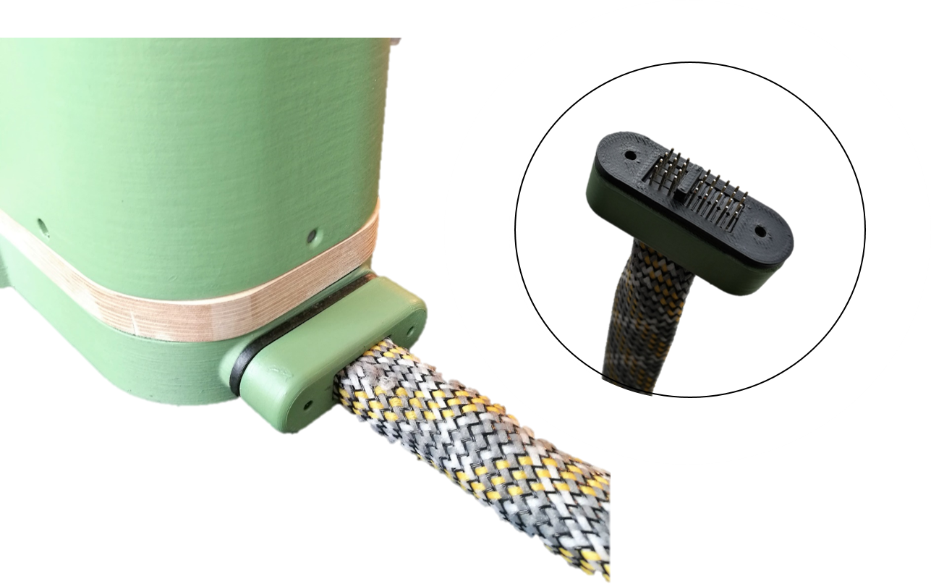
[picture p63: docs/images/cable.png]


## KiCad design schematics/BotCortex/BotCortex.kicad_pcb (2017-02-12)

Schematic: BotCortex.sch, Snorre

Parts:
1.2K1, 1.2K2, 1.2k1, 1.2k2: R; R4
C1: 47uF; C_Radial_D8_L13_P3.8
C2, C6, C12, C14, C16: 100nF; C_Disc_D3_P2.5
C3: 220uF; C_Radial_D5_L6_P2.5
C4, C5: 10uF; C_Radial_D5_L6_P2.5
C7: 47uF; C_Radial_D5_L6_P2.5
C11: 2200uF; C_Radial_D7.5_L11.2_P2.5
C13: 1000uF; C_Radial_D7.5_L11.2_P2.5
D1, D10: Diode; Diode_DO-35_SOD27_Horizontal_RM10
D5: 1N5822; Diode_DO-35_SOD27_Horizontal_RM10
F1: FUSE; FUSE_HOLDER
P1: 2x Serial; Socket_MOLEX-KK-RM2-54mm_Lock_5pin_straight
P2: Herkulex Servo; Molex_KK_6410-04
P3: Encoder Socket 1; Molex_KK_6410-04
P4: Encoder Socket 0; Molex_KK_6410-04
P5: Stepper Elbow; Molex_KK_6410-04
P6: Power In uC Servo 9V; bornier3
P7: Power Out uC Servo; Molex_KK_6410-03
P8: Stepper Forearm; Molex_KK_6410-04
P9: Stepper Wrist; Molex_KK_6410-04
P10: Stepper Upperarm; Molex_KK_6410-04
P11: Stepper Hip; Molex_KK_6410-04
P12: POWER_IN; bornier4
P13: PowerEnableIn; Molex_KK_6410-02
P14: Power Stepper 2; bornier2
P15: Power Stepper 3; bornier2
P16: Power Stepper 4; bornier2
P17: PowerEnableOut; Molex_KK_6410-02
P18: Power Stepper 5; bornier2
P19: Thermal Printer 5V; bornier2
P20: POTI 10K; Molex_KK_6410-03
P21: Reset_Conn; 1pin
P22: Reset Conn; 1pin
P23: LED-Driver-I2C; Molex_KK_6410-04
P24: UART6; PINHEAD1-2
P25: Thermal_Printer; Molex_KK_6410-04
P26: Reset Anschluss; Molex_KK_6410-03
P28: Power Stepper 1; bornier2
Q1, Q2: BC237; TO-92_Molded_Wide
R1: 220; R4
R5, R6: 120; R4
R8, R10: 1K; R4
REL1, REL2: Relay_1xON; RELAIS_HF115F
SW2: reset; SW_PUSH-12mm
U1: 7805; 78XX-TO-220
U2, U3: LM7809ACT; TO-220
U4: Teensy_3.5

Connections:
/3.3V: 1.2K1.1, 1.2K2.1, 1.2k1.1, 1.2k2.1, C16.1, P20.1, P25.4, U4.46 (3.3V_(250mA))
/5V: P12.3, P19.1
/12V: D5.2 (A), P12.2
/24V: F1.1, P12.1
/+5V: C7.1, P3.4, P4.4, P23.1, U1.VO, U4.48 (Vin_(3.3/5V))
/CLK0: P11.2, U4.6 (4/SDA2/PWM)
/CLK1: P10.2, U4.9 (7/SCL0/MOSI0/RX3/PWM)
/CLK2: P8.2, U4.12 (10/TX2/PWM)
/CLK3: P5.2, U4.17 (25)
/CLK4: P9.2, U4.20 (28/MOSI0)
/DIR0: P11.3, U4.7 (5/MISO1/TX1/PWM)
/DIR1: P10.3, U4.10 (8/SDA0/MISO0/TX3/PWM)
/DIR2: P8.3, U4.13 (11/MOSI0)
/DIR3: P5.3, U4.18 (26/SCL2/TX1)
/DIR4: P9.3, U4.21 (29/PWM)
/EN1: P10.4, U4.11 (9/RX2/PWM)
/EN2: P8.4, U4.14 (12/MISO0)
/EN3: P5.4, U4.19 (27/SCK0/RC1)
/EN4: P9.4, U4.22 (30/PWM)
/En0: P11.4, U4.8 (6/PWM)
/LoggerTX: P1.5, U4.24 (32/SCK1/TX4/A13)
/PowerOnServo: P17.2, R10.2
/PowerOnStepper: P17.1, R8.2
/PowerSupplyServo: P13.1, U4.44 (22/A8/PWM)
/PowerSupplyStepper: P13.2, U4.45 (23/A9/PWM)
/RESET: P21.1, P26.2, SW2.2
/RX5: P1.2, U4.26 (34/A15/SDA0/RX5)
/RX6: P24.2, P25.2
/Reset-LED: P26.3, R1.2
/SCl0: 1.2k1.2, P4.3, U4.41 (19/A5/SCL0)
/SCl1: 1.2K2.2, P3.3, P23.3, U4.29 (37/A18/PWM/SCL1)
/SDA0: 1.2k2.2, P4.2, U4.40 (18/A4/SDA0)
/SDA1: 1.2K1.2, P3.2, P23.2, U4.30 (38/A19/PWM/SDA1)
/TX5: P1.3, U4.25 (33/A14SCL0TX5)
/TX6: P24.1, P25.3
/VDDServo9V: P2.2, P6.3
/VDD_Servo_9V: P7.3, REL1.4
/VDD_uC_5V: C1.1, C2.1, C3.1, C6.1, P6.2, P7.2, U1.VI, U2.3 (OUT)
GNDPWR: C1.2, C2.2, C3.2, C6.2, C7.2, C11.2, C12.2, C13.2, C14.2, C16.2, P1.1, P2.1, P3.1, P4.1, P5.1, P6.1, P7.1, P8.1, P9.1, P10.1, P11.1, P12.4, P14.2, P15.2, P16.2, P18.2, P19.2, P20.3, P23.4, P25.1, P26.1, P28.2, Q1.3 (E), Q2.3 (E), SW2.1, U1.GND, U2.2 (GND), U3.2 (GND), U4.1 (GND), U4.34 (GND)
unnamed: C4.2, D10.1 (K), R5.1, REL2.2
unnamed: C5.2, D1.1 (K), R6.1, REL1.2
unnamed: C4.1, C5.1, C11.1, C12.1, D5.1 (K), R5.2, R6.2, U2.1 (IN), U3.1 (IN)
unnamed: C13.1, C14.1, REL1.3, U3.3 (OUT)
unnamed: D1.2 (A), Q1.1 (C), REL1.1
unnamed: D10.2 (A), Q2.1 (C), REL2.1
unnamed: F1.2, REL2.3
unnamed: P2.3, U4.2 (0/MOSI1/RX1)
unnamed: P2.4, U4.3 (1/MISO1/TX1)
unnamed: P14.1, P15.1, P16.1, P18.1, P28.1, REL2.4
unnamed: P20.2, U4.37 (15/A1)
unnamed: P22.1, U4.49 (Reset)
unnamed: Q1.2 (B), R8.1
unnamed: Q2.2 (B), R10.1
unnamed: R1.1, U4.27 (35/A16/PWM)

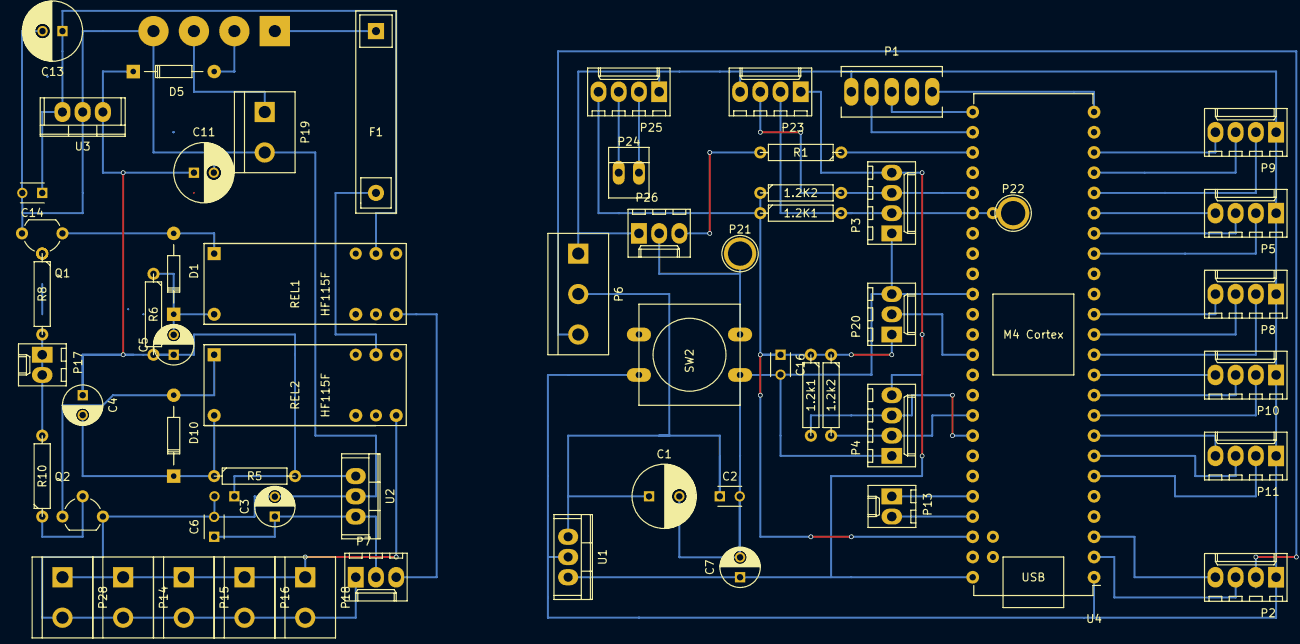
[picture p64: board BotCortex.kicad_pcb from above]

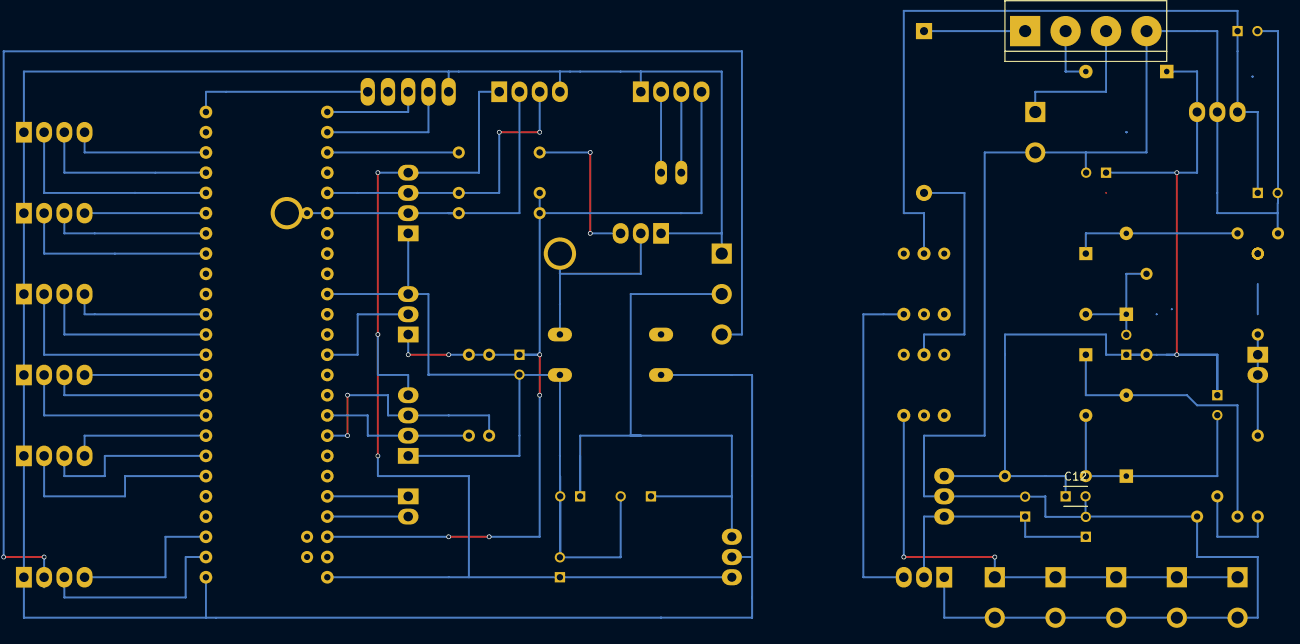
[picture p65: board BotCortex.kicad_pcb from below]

Board: 2 copper layers, 61 parts (2 on the bottom side), 54 nets.

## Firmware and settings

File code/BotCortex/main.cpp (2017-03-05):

#include <Arduino.h>
#include <Config.h>
#include <i2c_t3.h>
#include "watchdog.h"
#include "ams_as5048b.h"
#include "PatternBlinker.h"
#include <I2CPortScanner.h>
#include "AccelStepper.h"
#include <pins.h>
#include "hostCommunication.h"
#include "Controller.h"
#include "BotMemory.h"
#include "AMS_AS5048B.h"
#include "core.h"
#include "LightsController.h"
#include "Printer.h"

// global variables declared in pins.h
HardwareSerial* cmdSerial = &Serial5; 		// UART used to communicate with Cerebellum
HardwareSerial* logger = &Serial4;			// UART used to log
HardwareSerial* servoComm = &Serial1;		// UART used to communicate with the HerkuleX servos
HardwareSerial* printerComm = &Serial6;		// UART used to control the thermal printer

// rotary encoders are connected via I2C
i2c_t3* Wires[2] = { &Wire, &Wire1 };		// we have two I2C buses due to conflicting sensor addresses

// blinking patterns for LED on teensy board.
static uint8_t IdlePattern[2] = { 0b10000000, 0b00000000, };				// boring
static uint8_t DefaultPattern[3] = { 0b11001000, 0b00001100, 0b10000000 };	// nice!
static uint8_t LEDOnPattern[1] = { 0b11111111 };
static uint8_t LEDOffPattern[1] = { 0b00000000 };
PatternBlinker ledBlinker(LED_PIN, 100 /* ms */); // one bit in the patterns above is active for 100ms

void setCortexBoardLED(bool onOff) {
	// LEDs blinks a nice pattern during normal operations
	if (onOff)
		ledBlinker.set(LEDOnPattern,sizeof(LEDOnPattern));
	else
		ledBlinker.set(LEDOffPattern,sizeof(LEDOffPattern));
}

void setLEDPattern() {
	if (controller.isEnabled())
		ledBlinker.set(DefaultPattern,sizeof(DefaultPattern));
	else
		ledBlinker.set(IdlePattern,sizeof(IdlePattern));
}


// emergency method, that resets the I2C bus in case something went wrong (i.e. arbitration lost)
void resetI2CWhenNecessary(int ic2no) {
	if (Wires[ic2no]->status() != I2C_WAITING) {
		logger->println();

		switch(Wires[ic2no]->status())
		    {
		    case I2C_WAITING:  logger->print("I2C waiting, no errors "); break;
		    case I2C_ADDR_NAK: logger->print("Slave addr not acknowledged "); break;
		    case I2C_DATA_NAK: logger->print("Slave data not acknowledged "); break;
		    case I2C_ARB_LOST: logger->print("Bus Error: Arbitration Lost "); break;
		    case I2C_TIMEOUT:  logger->print("Bus Error: Time out "); break;
		    default:           logger->print("I2C busy "); break;
		}
		logger->print("I2C");
		logger->print(ic2no);
		logger->print(F("("));
		logger->print(Wires[ic2no]->status());
		logger->print(F(")"));

		Wires[ic2no]->resetBus();
		Wires[ic2no]->begin();
		Wires[ic2no]->setDefaultTimeout(1000);
		Wires[ic2no]->setRate(I2C_BUS_RATE);

		logger->print(F(" stat="));
		logger->println(Wires[ic2no]->status());
	}
}

void logPinAssignment() {
	logger->println("--- pin assignment");
	logger->print("knob                = ");
	logger->println(MOTOR_KNOB_PIN);
	logger->print("Power Stepper       = ");
	logger->println(POWER_SUPPLY_STEPPER_PIN);
	logger->print("Power servo         = ");
	logger->println(POWER_SUPPLY_SERVO_PIN);
	logger->print("PCB LED             = ");
	logger->println(LED_PIN);
	logger->print("Reset LED           = ");
	logger->println(RESET_LED_PIN);

	logger->print("Cmd     RX,TX       = (");
	logger->print(SERIAL_CMD_RX);
	logger->print(",");
	logger->print(SERIAL_CMD_RX);
	logger->println(")");
	logger->print("Logger  RX,TX       = (");
	logger->print(SERIAL_LOG_RX);
	logger->print(",");
	logger->print(SERIAL_LOG_RX);
	logger->println(")");
	logger->print("Herkulex RX,TX      = (");
	logger->print(HERKULEX_RX);
	logger->print(",");
	logger->print(HERKULEX_TX);
	logger->println(")");

	logger->print("Sensor0  SCL,SDA    = (");
	logger->print(SENSOR0_SCL);
	logger->print(",");
	logger->print(SENSOR0_SDA);
	logger->println(")");

	logger->print("Sensor1  SCL,SDA    = (");
	logger->print(SENSOR1_SCL);
	logger->print(",");
	logger->print(SENSOR1_SDA);
	logger->println(")");

	logger->print("Wrist En,Dir,CLK    = (");
	logger->print(WRIST_EN_PIN);
	logger->print(",");
	logger->print(WRIST_DIR_PIN);
	logger->print(",");
	logger->print(WRIST_CLK_PIN);
	logger->println(")");

	logger->print("Forearm En,Dir,CLK  = (");
	logger->print(FOREARM_EN_PIN);
	logger->print(",");
	logger->print(FOREARM_DIR_PIN);
	logger->print(",");
	logger->print(FOREARM_CLK_PIN);
	logger->println(")");

	logger->print("Elbow En,Dir,CLK    = (");
	logger->print(ELBOW_EN_PIN);
	logger->print(",");
	logger->print(ELBOW_DIR_PIN);
	logger->print(",");
	logger->print(ELBOW_CLK_PIN);
	logger->println(")");

	logger->print("Upperarm En,Dir,CLK = (");
	logger->print(UPPERARM_EN_PIN);
	logger->print(",");
	logger->print(UPPERARM_DIR_PIN);
	logger->print(",");
	logger->print(UPPERARM_CLK_PIN);
	logger->println(")");

	logger->print("Hip En,Dir,CLK      = (");
	logger->print(HIP_EN_PIN);
	logger->print(",");
	logger->print(HIP_DIR_PIN);
	logger->print(",");
	logger->print(HIP_CLK_PIN);
	logger->println(")");
}

void setup() {
	// until ledBlinker is initialized, switch turn on the LED.
	pinMode(LED_PIN, OUTPUT);
	digitalWrite(LED_PIN, HIGH);

	// the following is necessary to start the sensors properly
	// produce a LOW on i2c line to not confuse rotary encoders
	pinMode(PIN_SDA0, OUTPUT);
	digitalWrite(PIN_SDA0, HIGH);
	pinMode(PIN_SCL0, OUTPUT);
	digitalWrite(PIN_SCL0, HIGH);
	pinMode(PIN_SDA1, OUTPUT);
	digitalWrite(PIN_SDA1, HIGH);
	pinMode(PIN_SCL1, OUTPUT);
	digitalWrite(PIN_SCL1, HIGH);

	// LED within reset button
	pinMode(RESET_LED_PIN, OUTPUT);
	digitalWrite(RESET_LED_PIN, LOW);

	// disable power supply and enable/disable switch of all
	// motors, especially of steppers to avoid ticks during powering on.
	pinMode(POWER_SUPPLY_SERVO_PIN, OUTPUT);
	digitalWrite(POWER_SUPPLY_SERVO_PIN, LOW);
	pinMode(POWER_SUPPLY_STEPPER_PIN, OUTPUT);
	digitalWrite(POWER_SUPPLY_STEPPER_PIN, LOW);

	// Cant use controller.disable, since this requires a completed setup
	for (int i = 0;i<MAX_STEPPERS;i++) {
		pinMode(stepperSetup[i].enablePIN,OUTPUT);
		digitalWrite(stepperSetup[i].enablePIN, LOW);
	}

	// establish serial output and say hello
	cmdSerial->begin(CORTEX_COMMAND_BAUD_RATE);
	cmdSerial->println("WALTER's Cortex");

	// establish logging output
	logger->begin(CORTEX_LOGGER_BAUD_RATE);
	logger->println("--- logging ---");

	resetI2CWhenNecessary(0);	// check if I2c bus is fine. Restart if not.
	resetI2CWhenNecessary(1);

	// switch on servo to give them time to settle, while rest is initializing
	controller.switchServoPowerSupply(true); // works before being setup

	logPinAssignment();

	// lights console
	lights.setup();

	// initialize
	printer.setup();

	hostComm.setup();
	memory.setup();

	controller.setup();

	setWatchdogTimeout(2000);

	//done, start blinking
	ledBlinker.set(DefaultPattern, sizeof(DefaultPattern));

	// ready for input
	cmdSerial->print(F(">"));

	// read to be reset
	digitalWrite(RESET_LED_PIN, HIGH);
}


void loop() {
	watchdogReset();
	uint32_t now = millis();
	ledBlinker.loop(now);    	// LED on Teensy board
	hostComm.loop(now);			// wait for commands via serial interface
	memory.loop(now);			// check if something has to be written to EEPROM
	controller.loop(millis());	// run the actuators
	lights.loop(now);			// run the lights console

	if (controller.isSetup()) {
		resetI2CWhenNecessary(0);	// check if I2c bus is fine. Restart if not.
		resetI2CWhenNecessary(1);
	}
}

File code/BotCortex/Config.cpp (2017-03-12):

#include <Config.h>
#include "Arduino.h"
#include "BotMemory.h"
#include "utilities.h"
#include "pins.h"


void ActuatorConfig::setDefaults() {
	// Gripper (herkulex Servo)
	ActuatorConfig& gripper = memory.persMem.armConfig[GRIPPER];
	gripper.actuatorType = SERVO_TYPE;
	gripper.id = GRIPPER;
	gripper.config.servoArm.servo.id = GRIPPER;
	gripper.config.servoArm.servo.nullAngle = 33;
	gripper.config.servoArm.servo.minAngle= 0.0;
	gripper.config.servoArm.servo.maxAngle= 75.0;
	
	// Hand (herkulex Servo)
	ActuatorConfig& hand= memory.persMem.armConfig[HAND];
	hand.actuatorType = SERVO_TYPE;
	hand.id = HAND;
	hand.config.servoArm.servo.id = HAND;
	hand.config.servoArm.servo.nullAngle = 41;
	hand.config.servoArm.servo.minAngle= -120.0;
	hand.config.servoArm.servo.maxAngle= +120.0;
	
	// Wrist (stepper/Encoder)
	ActuatorConfig& wrist= memory.persMem.armConfig[WRIST];
	wrist.actuatorType = STEPPER_ENCODER_TYPE;
	wrist.id = WRIST;
	wrist.config.stepperArm.encoder.id = WRIST;
	wrist.config.stepperArm.stepper.id = WRIST;
	wrist.config.stepperArm.stepper.minAngle= -100.0;
	wrist.config.stepperArm.stepper.maxAngle= +90.0;
	wrist.config.stepperArm.stepper.maxAcc= 3000;
	wrist.config.stepperArm.stepper.maxSpeed= 140;
	wrist.config.stepperArm.encoder.nullAngle = -58.1;
	wrist.config.stepperArm.stepper.kP= 0.55;
	wrist.config.stepperArm.stepper.kD= 0.0;
	wrist.config.stepperArm.stepper.kI= 0.0;
	wrist.config.stepperArm.stepper.sampleRate= 20;
	wrist.config.stepperArm.stepper.microSteps = 8;
	
	// ellbow (stepper/Encoder)
	ActuatorConfig& ellbow= memory.persMem.armConfig[ELLBOW];
	ellbow.actuatorType = STEPPER_ENCODER_TYPE;
	ellbow.id = ELLBOW;
	ellbow.config.stepperArm.encoder.id = ELLBOW;
	ellbow.config.stepperArm.stepper.id = ELLBOW;
	ellbow.config.stepperArm.stepper.minAngle= -91.0;
	ellbow.config.stepperArm.stepper.maxAngle= +91.0;
	ellbow.config.stepperArm.encoder.nullAngle= 21.9;
	ellbow.config.stepperArm.stepper.maxAcc= 10000;
	ellbow.config.stepperArm.stepper.maxSpeed= 270;
	ellbow.config.stepperArm.stepper.kP= 0.50;
	ellbow.config.stepperArm.stepper.kD= 0.0;
	ellbow.config.stepperArm.stepper.kI= 0.0;
	ellbow.config.stepperArm.stepper.sampleRate= 20;
	ellbow.config.stepperArm.stepper.microSteps = 4;
	
	// forearm (stepper/Encoder)
	ActuatorConfig& forearm= memory.persMem.armConfig[FOREARM];
	forearm.actuatorType = STEPPER_ENCODER_TYPE;
	forearm.id = FOREARM;
	forearm.config.stepperArm.encoder.id = FOREARM;
	forearm.config.stepperArm.stepper.id = FOREARM;
	forearm.config.stepperArm.stepper.minAngle= -180.0;
	forearm.config.stepperArm.stepper.maxAngle= +34.0;
	forearm.config.stepperArm.encoder.nullAngle= 210.6;
	forearm.config.stepperArm.stepper.maxAcc= 1000;
	forearm.config.stepperArm.stepper.maxSpeed= 150;
	forearm.config.stepperArm.stepper.kP= 0.3;
	forearm.config.stepperArm.stepper.kD= 0.000;
	forearm.config.stepperArm.stepper.kI= 0.0;
	forearm.config.stepperArm.stepper.sampleRate= 20;
	forearm.config.stepperArm.stepper.microSteps = 8;


	// upperarm (stepper/Encoder)
	ActuatorConfig& upperarm= memory.persMem.armConfig[UPPERARM];
	upperarm.actuatorType = STEPPER_ENCODER_TYPE;
	upperarm.id = UPPERARM;
	upperarm.config.stepperArm.encoder.id = UPPERARM;
	upperarm.config.stepperArm.stepper.id = UPPERARM;
	upperarm.config.stepperArm.stepper.minAngle= -90.0;
	upperarm.config.stepperArm.stepper.maxAngle= +90.0;
	upperarm.config.stepperArm.encoder.nullAngle= 107.0;
	upperarm.config.stepperArm.stepper.maxAcc= 1000;
	upperarm.config.stepperArm.stepper.maxSpeed= 140;
	upperarm.config.stepperArm.stepper.kP= 0.5;
	upperarm.config.stepperArm.stepper.kD= 0.000;
	upperarm.config.stepperArm.stepper.kI= 0.0;
	upperarm.config.stepperArm.stepper.sampleRate= 20;
	upperarm.config.stepperArm.stepper.microSteps = 8;

	// Hip (stepper/Encoder)	
	ActuatorConfig& hip= memory.persMem.armConfig[HIP];
	hip.actuatorType = STEPPER_ENCODER_TYPE;
	hip.id = HIP;
	hip.config.stepperArm.encoder.id = HIP;
	hip.config.stepperArm.stepper.id = HIP;
	hip.config.stepperArm.stepper.minAngle= -90.0;
	hip.config.stepperArm.stepper.maxAngle= +90.0;
	hip.config.stepperArm.encoder.nullAngle= 143;
	hip.config.stepperArm.stepper.maxAcc= 700;
	hip.config.stepperArm.stepper.maxSpeed= 100;
	hip.config.stepperArm.stepper.kP= 0.4;
	hip.config.stepperArm.stepper.kD= 0.0;
	hip.config.stepperArm.stepper.kI= 0.0;
	hip.config.stepperArm.stepper.sampleRate= 20;
	hip.config.stepperArm.stepper.microSteps = 8;
}
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

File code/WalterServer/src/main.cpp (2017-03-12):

/*
 * main.cpp
 *
 * Webserver (Mongoose)
 *
 * Author: JochenAlt
 */

#include "mongoose.h" // mongoose MUST be first include, do not know why

#include "core.h"
#include "CmdDispatcher.h"
#include "Util.h"
#include "setup.h"

#include "logger.h"
INITIALIZE_EASYLOGGINGPP

static struct mg_serve_http_opts s_http_server_opts;

#include <stdlib.h>
#include <ctype.h>


// called when ^C is pressed
void signalHandler(int s){
	cout << "Signal " << s << ". Exiting";
	cout.flush();
	exit(1);
}

void setupLogger() {
	// setup logger
	el::Configurations defaultConf;
    defaultConf.setToDefault();
    defaultConf.set(el::Level::Error,el::ConfigurationType::Format, "%datetime %level [%func] [%loc] %msg");
    defaultConf.set(el::Level::Error, el::ConfigurationType::Filename, "logs/walter.log");

    defaultConf.set(el::Level::Info,el::ConfigurationType::Format, "%datetime %level %msg");
    defaultConf.set(el::Level::Info, el::ConfigurationType::Filename, "logs/walter.log");

    defaultConf.set(el::Level::Debug, el::ConfigurationType::ToStandardOutput,std::string("false"));
    // defaultConf.set(el::Level::Debug, el::ConfigurationType::Enabled,std::string("false"));

    defaultConf.set(el::Level::Debug, el::ConfigurationType::Format, std::string("%datetime %level [%func] [%loc] %msg"));
    defaultConf.set(el::Level::Debug, el::ConfigurationType::Filename, "logs/walter.log");

    // logging from uC is on level Trace
    defaultConf.set(el::Level::Trace, el::ConfigurationType::ToStandardOutput,std::string("false"));
    defaultConf.set(el::Level::Trace, el::ConfigurationType::Format, std::string("%datetime %level [uC] %msg"));
    defaultConf.set(el::Level::Trace, el::ConfigurationType::Filename, "logs/walter.log");

    el::Loggers::reconfigureLogger("default", defaultConf);

	LOG(INFO) << "Walter Website Setup";
}


// Define an event handler function
static void ev_handler(struct mg_connection *nc, int ev, void *ev_data)
{
    switch (ev)
    {
    	case MG_EV_HTTP_REQUEST: {
    			struct http_message *hm = (struct http_message *) ev_data;
    			string uri(hm->uri.p, hm->uri.len);
    			string query(hm->query_string.p, hm->query_string.len);
    	        string body(hm->body.p, hm->body.len);

    	        bool ok;
    			string response;
    			// if our dispatcher knows the command, it creates a response and returns true.
    			// Otherwise assume that we deliver static content.
    			bool processed = CommandDispatcher::getInstance().dispatch(uri, query, body, response, ok);
    			if (processed) {
    				if (ok) {
    					mg_printf(nc, "HTTP/1.1 200 OK\r\n"
    						"Content-Type: text/plain\r\n"
    						"Content-Length: %d\r\n\r\n%s",
    							(int) response.length(), response.c_str());
    				} else {
    					mg_printf(nc, "HTTP/1.1 500 Server Error\r\n"
    							"Content-Length: %d\r\n\r\n%s",
    							(int) response.length(), response.c_str());
    				}
    			} else {
    				// no API call, serve static content
    				mg_serve_http(nc, (http_message*) ev_data, s_http_server_opts);
    			}
    		break;
    	}
    default:
        break;
    }
}


int main(void) {
	struct mg_mgr mgr;
	struct mg_connection *nc = NULL;
	cs_stat_t st;

	mg_mgr_init(&mgr, NULL);


	// if we run on jochens notebook, use a different port than on Linux
	// (where the machine is occupied completely and we can use 8000)
#ifdef _WIN32
	#define SERVER_PORT WIN_WEB_SERVER_PORT
#else
	#define SERVER_PORT LINUX_WEB_SERVER_PORT
#endif


	string serverport_s = int_to_string(SERVER_PORT);
	nc = mg_bind(&mgr, serverport_s.c_str(), ev_handler);
	if (nc == NULL) {
		LOG(ERROR) << "Cannot bind to " << SERVER_PORT;
		exit(1);
	}

	// Set up HTTP server parameters
	mg_set_protocol_http_websocket(nc);
	s_http_server_opts.document_root = "web_root"; // Set up web root directory
	if (mg_stat(s_http_server_opts.document_root, &st) != 0) {
		LOG(ERROR) << "Cannot find web_root directory, exiting.";
		exit(1);
	}

	// catch SIGINT (ctrl-C)
    signal (SIGINT,signalHandler);

	// log into logs/walter.log
	setupLogger();

	// initialize kinematics and trajectory compilation
	Kinematics::getInstance().setup();

	// initialize communication to cortex
	bool cortexOk = false;

	LOG(INFO) << "Walter's webserver running on port " << SERVER_PORT;

	// ToDo change this loop to two threads running on different cores
	int lastTimeCortexSetup = millis();
	while (true) {
		if (cortexOk)
			TrajectoryExecution::getInstance().loop();
		else {
			if (millis()> lastTimeCortexSetup+1000 ) {
				cortexOk = TrajectoryExecution::getInstance().setup(CortexSampleRate);
				lastTimeCortexSetup = millis();
				if (cortexOk) {
					LOG(INFO) << "Cortex initialized successfully";
				} else {
					string error = getLastErrorMessage();
					LOG(ERROR) << "Communication with cortex failed (" << error.c_str();
					CommandDispatcher::getInstance().addAlert("communication with Walters cortex failed");
				}
			}
		}
		mg_mgr_poll(&mgr, 10); // check every 10ms for incoming requests
	}
	mg_mgr_free(&mgr);

	return 0;
}

/*


// central event handler of mongoose, all kinds of request go here
static void ev_handler(struct mg_connection *nc, int ev, void *ev_data) {
	struct http_message *hm = (struct http_message *) ev_data;
	switch (ev) {
	case MG_EV_HTTP_REQUEST: {
			string uri(hm->uri.p, hm->uri.len);
			string query(hm->query_string.p, hm->query_string.len);
	        string body(hm->body.p, hm->body.len);

	        bool ok;
			string response;
			// if our dispatcher knows the command, it creates a response and returns true.
			// Otherwise assume that we deliver static content.
			bool processed = CommandDispatcher::getInstance().dispatch(uri, query, body, response, ok);
			if (processed) {
				if (ok) {
					mg_printf(nc, "HTTP/1.1 200 OK\r\n"
						"Content-Type: text/plain\r\n"
						"Content-Length: %d\r\n\r\n%s",
							(int) response.length(), response.c_str());
				} else {
					mg_printf(nc, "HTTP/1.1 500 Server Error\r\n"
							"Content-Length: %d\r\n\r\n%s",
							(int) response.length(), response.c_str());
				}
			} else {
				// no API call, serve static content
				mg_serve_http(nc, (http_message*) ev_data, s_http_server_opts);
			}
		break;
	}
	default:
		break;
	}
}
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

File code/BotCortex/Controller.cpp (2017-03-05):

/* 
* Motors.cpp
*
* Created: 22.04.2016 19:26:44
* Author: JochenAlt
*/

#include "Arduino.h"
#include "utilities.h"
#include "BotMemory.h"
#include "Controller.h"
#include <I2CPortScanner.h>
#include "GearedStepperDrive.h"
#include "RotaryEncoder.h"
#include "watchdog.h"
#include "core.h"
#include "limits.h"
#include "LightsController.h"

Controller controller;
TimePassedBy servoLoopTimer;
TimePassedBy encoderLoopTimer;
bool adjustWhat = false;

// stepperloop needs to be called as often as possible, since the stepper impulse has to happen at 5000Hz at top speed
// So, call that whereever you can, even during delay() 
void plainStepperLoop() {
	controller.stepperLoop(); // take care that nothing happens inside until everything is properly initialized
}

// yield is called in delay(), used to leverage breaks during serial communication time
void yield() {
	controller.stepperLoop();
}

Controller::Controller()
{
	currentMotor = NULL;				// current motor used for manual control
	numberOfActuators = 0;				// number of motors that have been initialized
	numberOfEncoders = 0;				// number of rotary encoders that have been initialized
	numberOfSteppers = 0;				// number of steppers that have been initialized
	setuped= false;						// flag to indicate a finished setup (used in stepperloop())
	enabled = false;					// motors are disabled until explicitly enabled
}

void Controller::enable() {
	if (isSetup()) {
		for (int i = 0;i<numberOfActuators;i++) { 
			getActuator(i)->enable();
			// give it a break to not overload power supply by switching on all steppers at the same time
		}
		enabled = true;
	}
	lights.setEnableMode(enabled);

	// wait some time before starting the loop
	delay(10);
}

void Controller::disable() {
	if (isSetup()) {
		for (int i = 0;i<numberOfActuators;i++) {
			getActuator(i)->disable();
			// give it a break to not overload power supply by switching off all steppers at the same time
			delay(5);
		}
		enabled = false;
		lights.setEnableMode(enabled);
	}
}

void Controller::selectActuator(uint8_t no) {
	// disable other motors
	if (currentMotor != NULL) {
		currentMotor->disable();
		currentMotor = NULL;
	}
	
	if ((no>=0) || (no<MAX_ACTUATORS)) {
		currentMotor = getActuator(no);
		if (currentMotor != NULL)
			currentMotor->enable();
	} 
}

Actuator* Controller::getCurrentActuator() {
	return currentMotor;
}

void Controller::logConfiguration() {
	logger->println(F("ACTUATOR SETUP"));
	for (int i = 0;i<numberOfActuators;i++) {
		// ActuatorSetupData* thisActuatorSetup = &actuatorSetup[i];
		// ActuatorIdentifier id = thisActuatorSetup->id;
		//thisActuatorSetup->print();
		for (int j = 0;j<numberOfServos;j++) {
			ServoSetupData* thisServoSetup = &servoSetup[j];
			if (thisServoSetup->id == i) {
				logger->print(F("   "));
				thisServoSetup->print();
			}			
		}
		for (int j = 0;j<numberOfSteppers;j++) {
			StepperSetupData* thisStepperSetup = &stepperSetup[j];
			if (thisStepperSetup->id == i) {
				logger->print(F("   "));
				thisStepperSetup->print();
			}
		}
		for (int j = 0;j<numberOfEncoders;j++) {
			RotaryEncoderSetupData* thisEncoderSetup = &encoderSetup[j];
			if (thisEncoderSetup->id == i) {
				logger->print(F("   "));
				thisEncoderSetup->print();
			}
		}

	}
	
	logger->println(F("ACTUATOR CONFIG"));
	memory.println();
}

bool Controller::setup(bool force /* =false */) {
	switchServoPowerSupply(true);

	lights.setSetupMode(true);
	resetError();

	// reset any remains
	disable();
	// but leave power on if it is already

	if (memory.persMem.logSetup) {
		logger->println(F("--- switch on servo "));
	}

	// set the i2c lines to output to reset the sensors when starting up

	pinMode(PIN_SDA0, OUTPUT);
	digitalWrite(PIN_SDA0, HIGH);
	pinMode(PIN_SCL0, OUTPUT);
	digitalWrite(PIN_SCL0, HIGH);
	pinMode(PIN_SDA1, OUTPUT);
	digitalWrite(PIN_SDA1, HIGH);
	pinMode(PIN_SCL1, OUTPUT);
	digitalWrite(PIN_SCL1, HIGH);

	// necessary between switching on power supply on setting up serial communication
	// and giving rotary encoders some time to settle.
	delay(50);

	// reset number of correctly initialized devices
	numberOfSteppers = 0;
	numberOfEncoders = 0;
	numberOfServos = 0;

	if (memory.persMem.logSetup) {
		logger->println(F("--- I2C initialization"));
	}

	// initialize I2C0 and I2C1
	Wires[0]->begin();
	// timeout should be enough to repeat the sensor request within one sample
	// on I2C0 we have 4 clients (encoder of upperarm, forearm, elbow, wrist)
	// trial and error: 200ms is just not sufficient for AMS5048B to initialize
	Wires[0]->setDefaultTimeout(500 /* ms */);
	Wires[0]->setRate(I2C_BUS_RATE);

	Wires[1]->begin();
	// on I2C0 we have 2 clients  (hip encoder, LED driver)
	Wires[1]->setDefaultTimeout(500 /* ms */);
	Wires[1]->setRate(I2C_BUS_RATE);

	if (memory.persMem.logSetup) {
		logger->println(F("--- com to servo"));
	}

	HerkulexServoDrive::setupCommunication();

	if (memory.persMem.logSetup) {
		logger->println(F("--- initializing actuators"));
	}

	for (numberOfActuators = 0;numberOfActuators<MAX_ACTUATORS;numberOfActuators++) {
		watchdogReset(); // this takes a bit longer, kick the dog regularly

		if (memory.persMem.logSetup) {
			logger->print(F("--- setup "));
			logActuator((ActuatorIdentifier)numberOfActuators);
			logger->println(F(" ---"));
		}

		Actuator* thisActuator = &actuators[numberOfActuators];
		ActuatorConfig* thisActuatorConfig = &(memory.persMem.armConfig[numberOfActuators]);
		switch (thisActuatorConfig->actuatorType) {
		memory.persMem.armConfig[HIP].config.stepperArm.stepper.maxAngle= +90.0;
			case SERVO_TYPE: {
				if (numberOfServos >= MAX_SERVOS) {
					setError(MISCONFIG_TOO_MANY_SERVOS);
				}

				HerkulexServoDrive* servo = &servos[numberOfServos];
				servo->setup( &(memory.persMem.armConfig[numberOfActuators].config.servoArm.servo), &(servoSetup[numberOfServos]));
				thisActuator->setup(thisActuatorConfig, servo);

				lights.setActuatorMinMax(numberOfActuators, memory.persMem.armConfig[numberOfActuators].config.servoArm.servo.minAngle,memory.persMem.armConfig[numberOfActuators].config.servoArm.servo.maxAngle);

				numberOfServos++;

				if (thisActuator->hasStepper())
					setError(MISCONFIG_SERVO_WITH_STEPPER);
				if (thisActuator->hasEncoder())
					setError(MISCONFIG_SERVO_WITH_ENCODER);
				if (!thisActuator->hasServo())
					setError(MISCONFIG_SERVO);

				break;
			}

			case STEPPER_ENCODER_TYPE: {
				if (numberOfEncoders >= MAX_ENCODERS) {
					setError(MISCONFIG_TOO_MANY_ENCODERS);
				}
				if (numberOfSteppers >= MAX_STEPPERS) {
					setError(MISCONFIG_TOO_MANY_STEPPERS);
				}

				RotaryEncoder* encoder = &encoders[numberOfEncoders];
				GearedStepperDrive* stepper = &steppers[numberOfSteppers];
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

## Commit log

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2016-03-19 WristRot in Zylindrisch und Kugelig
    [BOM.xlsx]
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2016-03-20 Wrist2 begonnen mit engerem Bogen an der Weltraumkugel
    [BOM.xlsx]
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2016-03-27 Unterarm scheint einigermaßen fertig
    [BOM.xlsx]
2016-03-27 kleine verbesserungen an Forearm
    [BOM.xlsx]
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2016-04-08 Außenform von Schulter fertig
    [BOM.xlsx]
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2016-04-09 BOM für Schulter gemacht
    [BOM.xlsx]
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2016-04-15 Statt Drehkranz großes Rillenkugellager
    [BOM.xlsx]
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2016-04-15 Schraubenlänge im Grippermount korrigiert
    [BOM.xlsx]
2016-04-16 Unterarm hat nun Sensordeckel und Kabeldeckel mit Schrauben
    [BOM.xlsx]
2016-04-16 Bom kontrolliert und Lagersitz an Ellenbogen fester gemacht
    [BOM.xlsx]
2016-04-16 zahnriemen für Hüfte jetzt drin
    [BOM.xlsx]
2016-04-16 Lagerklemme bei Handgelenk probiert
    [BOM.xlsx]
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2016-04-17 Servobefestigung korrigiert
2016-04-17 HerkuleX servo mit M2 Schrauben befestigt (M3 war falsch)
    [BOM.xlsx]
2016-04-17 Lagervielfalt reduziert und Riemenspanner im Ellbogen als Druckteil
    [BOM.xlsx]
2016-04-17 Schulter Riemenspanner enger und gleichförmig gemacht
    [BOM.xlsx]
2016-04-18 Schraubenlängen korrigiert
    [BOM.xlsx]
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2016-04-22 Shopping einsortiert und blind den uC getippt
    [BOM.xlsx]
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2016-04-26 RiemenSpanner nachgemessen und korrigiert
    [BOM.xlsx]
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2016-04-30 Stepper Motor läuft mit Pibot treiber
    [BotController.sch]
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2016-05-01 AMS Sensor code als Lib
    [BOM.xlsx, BotController.sch]
2016-05-05 Rotary Encoder mit gleicher I2c Adresse angesprochen
    [BOM.xlsx, BotController.sch, handgelenk-korpus.stl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]
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2016-05-18 Unterarm bekam neue Grundform
    [BOM.xlsx]
2016-05-21 Unterarm mit neuem getriebe
    [BOM.xlsx]
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2016-05-22 Die Zahnriemen im Ellbogen verbessert
    [BOM.xlsx]
2016-06-04 Null stellung von Encoders gemacht Plausi Check
    [BOM.xlsx]
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2016-06-06 Unterarm links neu gedruckt mit verbesserter Kabelführung
    [BOM.xlsx]
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2016-06-15 hand sieht gut aus
    [BOM.xlsx]
2016-06-16 Handgreifer etwas fetter und runder gemacht
    [BOM.xlsx]
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2016-06-19 Lager in Hand vergrößert, weil die 6mm Lager in der Kneipe zerbrochen sind
    [BOM.xlsx]
2016-06-24 beide Servos angesteuert und Handflansch korrigiert
    [BotController.kicad_pcb, BotController.sch]
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2016-06-26 Am Ellbogen kleinere Lager bei den Riemenspannern
    [Zortrax.xlsx]
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2016-07-01 Ellbogen montiert und korrigiert
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2016-07-02 Ellbogen jetzt ohne Motorloch, weil 26Ncm Motor reicht und nach innen verschoben werden konnte
    [BOM.xlsx]
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2016-07-03 PCB bekommt die letzten 4 PINs als enhancement Stecker Handgelenk vom Rest des entfernbaren Motordecksl bereinigt
    [BOM.xlsx, BotController.kicad_pcb, BotController.sch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]
2016-07-04 Ellenbogen gedruckt und Schaltung mit PowerSupply gemacht
    [BotController.kicad_pcb, BotController.sch, BotPowerBoard.sch]
2016-07-08 HostCommunication scheint zu gehen
    [BotController.kicad_pcb, BotController.sch, Kinematik.xlsx]
2016-07-09 stepper geht jetzt wieder
    [BOM.xlsx, BotController.kicad_pcb, BotController.sch]
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2016-07-16 kleine Korrekturen beim Ellbogen und unterarm
    [BotController.kicad_pcb, BotController.sch]
2016-07-17 Korrekturen am Oberarm nach erster Passung
    [BOM.xlsx, BotController.sch]
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2016-07-22 Motorraum in Oberraum war 0,5 mm zu eng
    [Kinematik.xlsx]
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2016-07-30 Kabelstütze mit mehr findament
    [BOM.xlsx]
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2016-08-01 Neuer Oberarm mit horizontalem Riemenspanner
    [BOM.xlsx, BotController.kicad_pcb]
2016-08-04 GLUI2 ausgebaut (zu hässlich) auf GLUI umgestiegen
    [g2Blue.cfg, g2Default.cfg]
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2016-08-11 rotated gripper view to make it more handy
    [Kinematik.xlsx]
2016-08-12 fixed ugly bug in kinematics when the upper angles have an infinite number of solution
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2016-08-17 kinematic pole problem solved
    [HandKonstruktionsSkizze.0002.ipt]
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2016-08-19 Upperarm tested, 1/16 microsteps
    [BOM.xlsx]
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2016-08-22 load&save&merge & kinematik avoiding poles
    [Trajectory.cpp]
2016-08-22 Shoulder korrigiert und doku
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2016-08-25 pole in kinematics solved
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2016-08-27 More torque for the shoulder
    [BOM.xlsx, Kinematik.xlsx]
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2016-09-03 fix strings with white space were not serialized correctly
    [Trajectory.cpp]
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2016-09-04 Fix in Trajectory Execution and printed shoulder base
    [BOM.xlsx]
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2016-09-08 changed trajectory input from duration to speed
    [Kinematik.xlsx]
2016-09-08 Fix: fixed limit of trajectory speed
    [Trajectory.cpp]
2016-09-09 fix: end node of trajectory now at endtime and not above
    [Kinematik.xlsx]
2016-09-10 fix in speed profile
    [Kinematik.xlsx]
2016-09-11 Fixed Beziercurve::curvelength of angle interpolation
    [Kinematik.xlsx]
2016-09-11 save trajectory fixed
    [BOM.xlsx, Kinematik.xlsx]
2016-09-14 Speed profile completely reworked
    [Kinematik.xlsx]
2016-09-15 Fix: bug in speed computation
    [Trajectory.cpp]
2016-09-15 Bugfxi in negative trapez profile
    [Kinematik.xlsx]
2016-09-15 fixed lazyramp bug
    [Kinematik.xlsx]
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2016-09-18 adaped acceleration of hip
    [BOM.xlsx]
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2016-10-02 Walter shcon ganz gut
    [BOM.xlsx, Zahnriemenrad T5 12Z.stp]
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2016-10-22 hand wieder mit beule und unterarm angepasst
    [BOM.xlsx]
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2016-10-24 neuer Versuch der Hand ohne Beule, Servo jetzt axial
    [Zahnriemenrad T5 32Z.stp]
2016-10-26 new font for walter, new riemenspanner
    [BOM.xlsx]
2016-10-26 left side's bearing holder was 1mm too low
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2016-10-27 fehlendes 6-kant schraubenloch in Hüftbasis reingesetzt und Magnetposition korrigiert.
2016-10-29 Forearm's motor moved 1mm down
    [BOM.xlsx]
2016-10-29 flansch im ellenbogen 15Z statt 14Z
    [BOM.xlsx, Zahnriemenrad T2.5 15Z.stp]
2016-10-30 forearm with 245 belt (instead of 250mm)
    [BOM.xlsx]
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2016-11-04 Unterarm Kabelkanal etwas größer, Kabeldeckel eingeführt und Zahnriemenraddurchbruch
    [BOM.xlsx]
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2016-11-13 Oberarm fertig für druck
    [BOM.xlsx]
2016-11-14 Oberarm lagerring an der Seite hat jetzt keine durchgehenden Schlitz mehr
    [BOM.xlsx]
2016-11-20 connect To Bot mode
    [BOM.xlsx]
2016-11-20 interface to uC converts from radian to degrees
    [BOM.xlsx]
2016-11-24 glui bitmaps did not work anymore, replaced by opengl
    [ActuatorCtrlInterface.cpp]
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2016-11-26 Servos return angle now (bugfix)
    [Config.cpp, GearedStepperDrive.cpp, GearedStepperDrive.h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]
2016-11-27 timeouts corrected, timings adapted, startup and teardown works no. PID still missing
    [ActuatorCtrlInterface.cpp, Controller.cpp, GearedStepperDrive.cpp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]
2016-12-02 einzelne Motoren Regelung eingestellt
    [BOM.xlsx, BotController.kicad_pcb]
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2016-12-07 Trajectory planning now works with movements haveing changes in orientation only
    [BOM.xlsx]
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2016-12-09 introduced automatic retry with timeout after communicaiton failre
    [BOM.xlsx]
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2016-12-10 fixed controller loop issue
    [Controller.cpp]
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2016-12-24 PCB ready and eeprom bug fixed
    [Config.cpp, Controller.cpp, main.cpp]
2016-12-24 AS5048 require 5V, 3.3 V is not stable. PCB changed.
    [BotCortex.kicad_pcb, BotCortex.sch]
2016-12-24 I2C problems are fixed now, seems to work stable. Amended documentation
    [BotController.kicad_pcb, BotController.sch, BotCortex.kicad_pcb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]
2016-12-25 shit.broke a sensor.
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2016-12-29 webserver error handling done
    [Actuator.cpp, Config.cpp, Config.h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]
2016-12-29 fixed many bugs
    [BOM.xlsx, BotCortex.sch]
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2017-01-01 moved I2C initialization into setup (when I2C line hangs, setup has not been sufficient but the cortex had to be reset)
    [Controller.cpp]
2017-01-01 configuration changes due to new motor in writs, new gears in upperarm and forearm
    [BOM.xlsx]
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2017-01-13 reset to working state
    [Config.cpp, Controller.cpp, GearedStepperDrive.cpp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]
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2017-01-16 Bugfix: at the end of a trajectory, current position was nulled (= invalid) and displayed
2017-01-16 Bugfix in Kinematic isSolutionValid
    [Config.cpp, Trajectory.cpp]
2017-01-16 Bugfix: floatprecision was not used in marshalling floats
    [Trajectory.cpp]
2017-01-18 Bugfix: Negative Ramp profile computed positive t1
    [Trajectory.cpp]
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2017-01-26 BugFix in SpeedProfile removed Mixed view in UI added handview panel in UI
    [Kinematik.xlsx]
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2017-01-28 added Reset LED to schematics and Cortex
    [BotCortex.kicad_pcb, BotCortex.sch]
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2017-01-29 Bugfix: power /enable/setup LEDs were not displayed during setup phase
    [LightsController.cpp]
2017-02-03 Bugfix: Post request with Poco requires "content-length" of body
    [main.cpp]
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2017-02-04 i2c pullup resistor reduced to 1.1K since i2c lines capacity was 400pF
    [BotCortex.sch]
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2017-02-04 Bugfix in Adafruits Library for Tiny Thermal Printer: UpsideDown sent wrong esc sequence
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2017-02-05 bugfix: mongoose.h must be first include. Otherwise strange SEGV happen
    [main.cpp]
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2017-02-09 new feature: trajectory nodes without a name are given a number
    [BOM.xlsx]
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2017-02-11 cortex socket was too tight
2017-02-12 Bugfix: If lIghtscontroller not connected cortex was stuck
    [Controller.cpp, LightsController.cpp, main.cpp]
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2017-02-18 corrected bug in visualization of gripper
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2017-02-18 Bug: when encoder was down, stepper turned in wrong direction
    [GearedStepperDrive.cpp]
2017-02-18 corrected wrong dimensions of gripper
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2017-02-25 new cortex command "setup force" to leave power on even if errors occur
    [Controller.cpp]
2017-03-11 Towers of Hanoi work now and some bugfixes
    [Config.cpp, Config.h]
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2017-03-11 Serious Bug in Kinematics: wrong sign in angle4, strange enough the downstream selection of solutions compensated that
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2017-03-12 bug in kinematic found
    [Kinematik.xlsx]
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

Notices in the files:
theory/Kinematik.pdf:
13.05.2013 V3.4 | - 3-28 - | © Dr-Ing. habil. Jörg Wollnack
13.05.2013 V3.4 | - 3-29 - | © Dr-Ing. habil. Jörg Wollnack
